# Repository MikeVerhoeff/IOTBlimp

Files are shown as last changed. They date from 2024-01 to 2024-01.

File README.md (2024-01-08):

# Folder Content

### /ArduinoExperimentCollection
- Java project to communicate with Adruino, and quickly plot the results
- Build with Maven and uses JavaFX and jSerialComm
- To run in Intellij open the Maven tab and run ArduinoExperimentCollection --> Plugins --> javafx --> javafx:run
- or run ```mvn clean javafx:run```

### /ArduinoExperimentCollection/scripts
- Python scripts that get run when data has been collected via the ui

### /ArduinoExperimentCollection/sensors
- Arduino project that implements the balloon failure detection

### /ArduinoExperimentCollection/ResultsIndex.ods
- Spreadsheet that has most/all the experiment that we did and where the data is stored

### /ArduinoExperimentCollection/scripts/overview/distrib2.py
- Script to generate plots

### /Sound detection 
- Scripts for testing the filter applied to the microphone

### /CAD
- 3D Model of the blimp drone mechanism

# Overview of Failure Detection Arduino Project

## Data Structures (SensorInterface.h)

For each set of sensors there is a SensorInterface that defines:
* a unique key (char), used in communication with UI
* a recognizable name of the group of sensors, displayed in UI
* a threshold value for when the balloon failure has to be triggered
* a function to initialize the sensors
* a function to stop the sensors
* a array (and its length) of TestInfo structs for each individual sensor

The TestInfo struct contains:
* function that returns current sensor value (short)
* values to construct the activation function (on, off, off2, on2, useonoff2)
* the weight of this sensor during fusion
* the time the highest value has to be held (hold_time)
* other values that get set and updated during detection(on_time, last_value, used_last_value)

## Detection loop (Settings.h)

The main loop for detecting balloon failure is in:

```void Settings.run_times(unsigned long n)```

This function runs the detection loop n times or forever if n=0 at the frequency that has been set before (default 175 Hz). It also turns on the LED when balloon failure has been detected and triggers the blimp to drone transformation.
It used ```short TestInfo.run(unsigned long current_time)``` to get the sensor value after passing through the activation function, and apply the hold time.

## General
```sensors.ino``` sets up all the sets of sensors that can be used and communicates with the UI.
```accelerometer.h```, ```gyroscope.h```, ```piezo.h```, ```proximity_sensor.h``` and ```microphone.h``` implement function to initialize, pole and stop the sensors. ```record.h``` has helper functions for printing results, and ```transform.h``` handles the servo that controls the clutch that caused the transformation when released.

# Overview of Data Collection UI

![image](UI.png)

The fist field "Python" sets the command used to execute the scripts in the directory set by "Script Directory".
The field "Data Directory" says where the results should be stored. "Experiment name" indicates how to name the folder with the results, if this field is left empty only a file with named with the current time is stored. If a Folder with the experiment name already exists "_(n)" is appended.

The dropdown box shows all serial interfaces after scanning. After connecting the next fields show up.
"Start Delay" sets a delay between pressing the start button and the start command being send.
After scanning "interface" selects which set of sensors(SensorInterface) to run.
"Frequency" sets and shows the frequency at which the sensors are checked.
"Time / Count" indicates how long to run the detection for. In "Time / (Count)" mode this value is in seconds, in "(Time) / Count" mode this value is in number of loops, in this mode if the value is set to 0 it will only stop when the stop button is pressed.

The Text Area "Serial" gets filled with the serial data the arduino sends after the it has indicated that it is done with the detection. The Text Area "Python" has the console output of the scripts, and gets all the images the scripts generate in there working directory.

## Command line arguments for scripts

Count: ```<python> <script file> <data file> -f <frequency> -c <count> -i <interface name>```

Time: ```<python> <script file> <data file> -f <frequency> -t <time> -i <interface name>```

# Plotting script

The plotting script `ArduinoExperimentCollection/scripts/overview/distrib2.py` can be used to generate plots used in the report for a specific sensor or quickly generate a plot for other data.
To generate the plots from the report run:
```
python distrib2.py MIC
python distrib2.py ACC
python distrib2.py PIEZO
python distrib2.py PROX
python distrib2.py FUSION
```
To generate other plots use:
```
python distrib.py <folder> <partial experiment name> <sensor name> <vals/max/min> ["filter"/no] [x label] [y label]
```
for example to plot the maximal values we got during our tests of fusion:
```
python distrib.py ../../pop fusion P_X max no "activation sum" "count / total"
```
This will get all the data from 'fusion', 'fusion_(1)', ..., 'fusion_(9)'.

This scrips also has some settings that can be set in the file:
```
hideHists = False      # don't display the histograms, only fit normal distributions
hideFit = True         # don't display 
dontShow = False       # don't open the graph in a window only store it
cumulative = True      # make a cumulative distribution from the histogram
showActivation = False # add the activation function
```

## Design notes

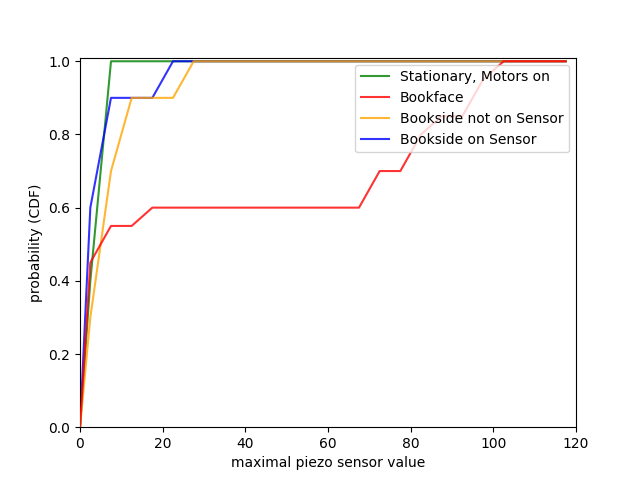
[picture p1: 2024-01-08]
ArduinoExperimentCollection/scripts/overview/hists/cdf/piezo_book_2.png

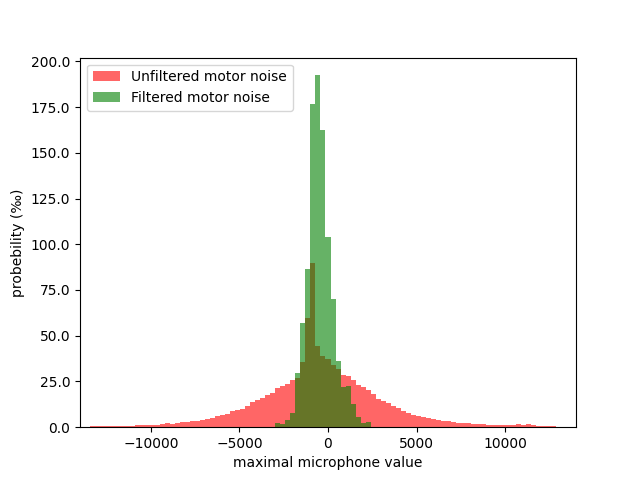
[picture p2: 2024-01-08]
ArduinoExperimentCollection/scripts/overview/hists/mic_noize.png

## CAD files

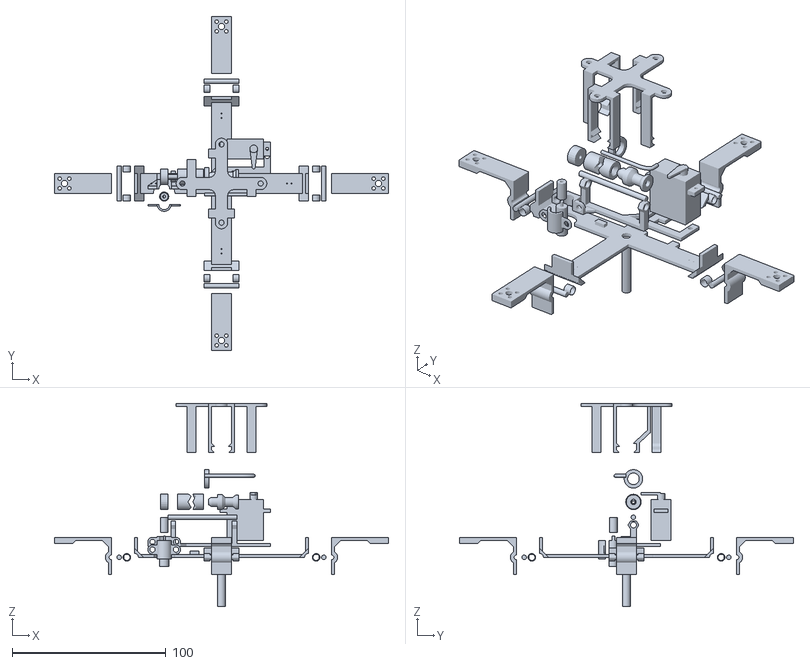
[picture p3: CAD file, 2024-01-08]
CAD/BlimpCoupling2_exploded.stl
217.0 x 217.0 x 132.0

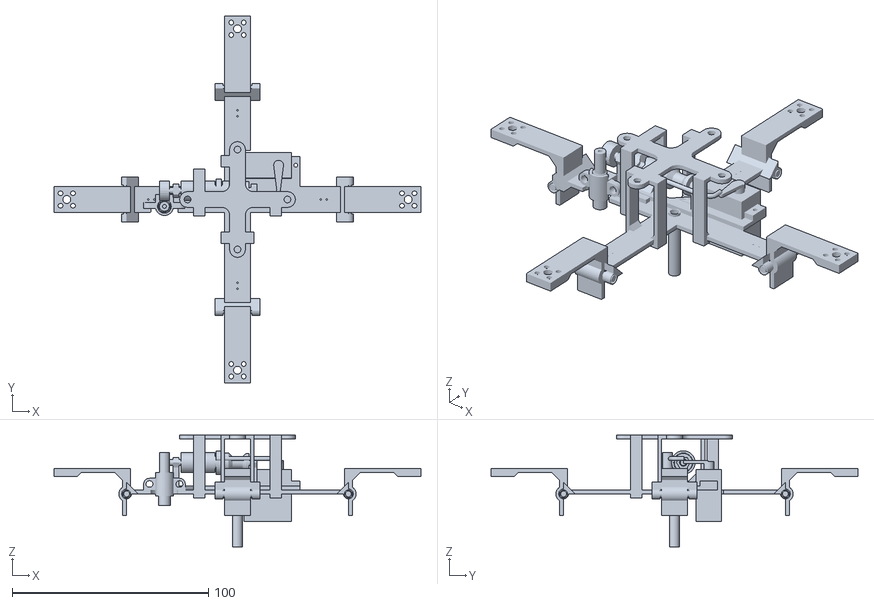
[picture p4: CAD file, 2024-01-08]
CAD/BlimpCoupling2.stl
187.0 x 187.0 x 57.0

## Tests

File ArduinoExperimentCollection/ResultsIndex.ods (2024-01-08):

Folder | Name | Description | balloon | Sensor | Graph
acc | fp_1ms_side | Moving drone side to side hanging on a string, abbout 1m/s, moving with arm | latex 30cm | ACC | Accelerometer: Movement
acc | fp_1ms_up_down | Moving drone up and down hanging on a string, moving with arm | latex 30cm | ACC | Accelerometer: Movement - Accelerometer: Pop
dataMic | 30cm_pop_filtered | Pop 21cm latex balllon 40 cm away | latex 50cm | MIC (f) | Microphone: Pop Balloon at Diffrent Distances
dataMic | 150cm_pop_filtered | Pop 21cm latex balllon 150 cm away | latex 50cm | MIC (f) | Microphone: Pop Balloon at Diffrent Distances
dataMic | 300hz_filtered | Play 300Hz tone on phone close above the microphone | none | MIC (f) | Microphone: Pop Balloon at Diffrent Distances
dataMic | still_filtered | Recording of quite room as baselline | none | MIC (f) | Microphone: Pop Balloon at Diffrent Distances
dataPartyBalloonPiezo\100K-PiezoFlex | * | Noticed the piezo has brocken, just recorded noize | latex 21cm | PIEZO
dataPartyBalloonPiezo\100K-PiozoHard-tapenormal | * | Prelimenary tests for the reenforced piezo sensor with 100K ohm resistor | latex 21cm | PIEZO | Piezo: Effect of Parallel Resistance(PiezoH_pop_(2), PiezoH_1M_pop) - Piezo: Hitting ballon in diffrent positions(PiezoH_pop) - Piezo: Distributions Scaled to Same Hieght(PiezoH_pop)
dataPartyBalloonPiezo\50K-PiozoHard-tapenormal | * | Prelimenary tests for the reenforced piezo sensor with 100K ohm resistor | latex 21cm | PIEZO | Piezo: Effect of Parallel Resistance(PiezoH_pop_(3))
dataPiezo | nerf_direct_hit | Shooting nerf disk at piezo sensor fixed to balloon | latex 50cm | PIEZO | Piezo: Hitting ballon in diffrent positions - Piezo: Distributions Scaled to Same Hieght
dataPiezo | nerf_disk_side | Shooting nerf disk at balloon, not hitting close to sensor | latex 50cm | PIEZO | Piezo: Hitting ballon in diffrent positions - Piezo: Distributions Scaled to Same Hieght
dataPiezo | still | Piezo sensor fixed to balloon, nothing happening | latex 50cm | PIEZO | Piezo: Maximal Value From 10 Runs: Still vs Vibrations - Piezo: Book Hits - Piezo: Distributions Scaled to Same Hieght
dataPiezo | vibration_dremel_5t | Using a dremmel set to 5000 rpm, with an uneven weighted attatchement to make the balloon vibrate | latex 50cm | PIEZO | Piezo: Maximal Value From 10 Runs: Still vs Vibrations
dataProx | baseline_absent | Recording sensor data without a balloon present | none | PROX | Proximity Balloon: Present vs Absent - Proximity Balloon: Absent - Proximity Balloon: Absent vs IR LED
dataProx | baseline_absent_<x> | Recording sensor data without a balloon present, but under specific lighting conditions <x> | none | PROX | Proximity Balloon: Present vs Absent - Proximity Balloon: Absent - Proximity Balloon: Absent vs IR LED
dataProx | gray_baseline_present | Recording sensor data with balloon present, and undisurbed | latex 50cm gray | PROX | Proximity Balloon: Present vs Absent - Proximity Balloon: Present vs Weaving Object
dataProx | gray_IR_LED_direct_full | https://www.adafruit.com/product/387 @ 1.6v pointing at arduino from just above it | latex 50cm gray | PROX | Proximity Balloon: Absent vs IR LED
dataProx | gray_IR_LED_indirect | https://www.adafruit.com/product/387 @ 1.6v pointing at the balloon just above the arduino | latex 50cm gray | PROX
dataProx | gray_stick | Move varius objects just above the sensor | latex 50cm gray | PROX | Proximity Balloon: Absent vs IR LED
dataProx | IR_LED_direct_under_powered | https://www.adafruit.com/product/387 @ 1.5v pointing at arduino from just above it | none | PROX | Proximity Balloon: Present vs Weaving Object
fp | 30cm_pop_filtered | Pop 21cm latex balllon 40 cm away | latex 50cm | MIC (f) | Microphone: Pop Balloon at Diffrent Distances
fp | 150cm_pop_filtered | Pop 21cm latex balllon 150 cm away | latex 50cm | MIC (f) | Microphone: Pop Balloon at Diffrent Distances
fp | black_plastic | Move black cap of super glue above sensor | latex 50cm gray | PROX | Proximity Balloon: Present vs Weaving Object
fp | permanent_marker | Move black whiteboard marker cap just above the sensor | latex 50cm gray | PROX | Proximity Balloon: Present vs Weaving Object - Proximity Balloon: Example of whiteboard marker interfearing(2)
fp | scissor | Move scissor just above the sensor | latex 50cm gray | PROX | Proximity Balloon: Present vs Weaving Object
fp | stick | Move satay sticks just above the sensor | latex 50cm gray | PROX | Proximity Balloon: Present vs Weaving Object
fp_tests | baseline_motor | Motors on at 50 or 60% recording all sensors, beging held still by holding balloon | tpu 21 inch | all | Piezo: Maximal Value From 10 Runs: Still vs Vibrations - Piezo: Distributions Scaled to Same Hieght - Accelerometer: Movement - Accelerometer: Pop
fp_tests | fp_1m | Pop 21cm latex balllon 1 m away | tpu 21 inch | MIC (r)
fp_tests | fp_10cm | Pop 21cm latex balllon 10 cm away | tpu 21 inch | MIC (r)
fp_tests | fp_black | Move black ballon up and down above sensor | latex 21cm | PROX
fp_tests | fp_gray | Move gray ballon up and down above sensor | latex 21cm | PROX
fp_tests | fp_red | Move red ballon up and down above sensor | latex 21cm | PROX | Proximity Balloon: Raise and Lower(6)
fp_tests | fp_transparent | Move transparent tpu ballon up and down above sensor | tpu 21 inch | PROX
fp_tests | fp_transparent_edge | Move transparent tpu ballon up and down above sensor, rotated that edge of ballon gows over sensor | tpu 21 inch | PROX | Proximity Balloon: Raise and Lower(5)
fp_tests | fp_transparent_blue | Move blue ballon up and down above sensor | latex 21cm | PROX
fp_tests | fp_white | Move white ballon up and down above sensor | latex 21cm | PROX
fp_tests | fp_mirror_angle | Move mirror up and down above sensor at 45 degree angle, so light is reflected away | none | PROX | Proximity Balloon: Raise and Lower(7)
fp_tests | fp_mirror_flat | Move mirror up and down above sensorf face down, so light is reflected back | none | PROX
fp_tests | fp_nerf_on | Shooting nerf disk at piezo sensor fixed to balloon | tpu 21 inch | PIEZO, ACC | Accelerometer: Movement
fp_tests | fp_nerf_non | Shooting nerf disk at balloon, not hitting close to sensor | tpu 21 inch | PIEZO, ACC | Accelerometer: Movement
fp_tests | fp_bookface_soft | Hitting ballon with the face of a book, random position | tpu 21 inch | PIEZO, ACC | Piezo: Book Hits - Accelerometer: Movement
fp_tests | fp_bookside_non | Hitting ballon with the face of a book, random position, but not on piezo sensor | tpu 21 inch | PIEZO, ACC | Piezo: Book Hits - Accelerometer: Movement
fp_tests | fp_bookside_on | Hitting ballon with the face of a book, close to piezo sensor | tpu 21 inch | PIEZO, ACC | Piezo: Book Hits - Accelerometer: Movement
pop | acc | Pop balloon to determine responce time | latex 50cm | ACC | Accelerometer: Pop
pop | mic | Pop balloon to determine responce time | latex 50cm | MIC (f) | Microphone: Pop Balloon at Diffrent Distances
pop | piezo | Pop balloon to determine responce time | latex 50cm | PIEZO | Piezo: Hitting ballon in diffrent positions
pop | fusion | Pop balloon to determine responce time and reliability of fusion | latex 50cm | PIEZO(breaking), ACC, PROX | Piezo: Hitting ballon in diffrent positions, Accelerometer: Pop
pop | all | Pop balloon to determine fusion weight | latex 50cm | all (PIEZO is breaking) | Proximity Balloon: Examples of popping(1, 7, 8) - Accelerometer: Pop - Microphone: Pop Balloon at Diffrent Distances - Piezo: Hitting ballon in diffrent positions
pop | "all", "all_(3)", "all_(4)" | Pop balloon to determine fusion weight | latex 30cm | all (PIEZO is breaking) | Accelerometer: Pop - Microphone: Pop Balloon at Diffrent Distances
pop | all_small | Pop balloon to determine fusion weight | latex 21cm | all | Microphone: Pop Balloon at Diffrent Distances
prelim_tests | pie_face_hard_non |  | tpu 21 inch | PIEZO
prelim_tests | pie_face_soft_non |  | tpu 21 inch | PIEZO
prelim_tests | pie_motor_side |  | tpu 21 inch | PIEZO
prelim_tests | pie_motor_side_tran |  | tpu 21 inch | PIEZO
prelim_tests | pie_motor_side45 |  | tpu 21 inch | PIEZO
prelim_tests | pie_nerf_dart_non | Shoot nerf dart at senor point blank | tpu 21 inch | PIEZO
prelim_tests | pie_nerf_dart_non_soft | Shoot nerf dart at senor further away | tpu 21 inch | PIEZO
prelim_tests | pie_nerf_disk_non_hard | Shoot nerf disk at senor point blank | tpu 21 inch | PIEZO
prelim_tests | pie_nerf_disk_on_hard | Shoot nerf disk at senor further away | tpu 21 inch | PIEZO
prelim_tests | pie_pop | Pop tpu balloon | tpu 21 inch | PIEZO
prelim_tests | pie_side_hard_non |  | tpu 21 inch | PIEZO
prelim_tests | pie_side_soft_non |  | tpu 21 inch | PIEZO
prelim_tests | prox_tran_test |  | tpu 21 inch | PROX
small_pop | p_not_stuck | Ballon pop not taped to drone | latex 21cm | PIEZO
small_pop | piezo | Ballon pop taped to drone | latex 21cm | PIEZO

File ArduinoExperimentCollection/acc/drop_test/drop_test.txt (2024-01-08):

P_X:
0
0
0
0
0
0
0
0
0
0
0
0
0
0
0
0
0
0
0
0
0
0
0
0
0
0
0
0
0
0
0
0
0
0
0
0
0
0
0
0
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
ACC_X:
0.17
0.17
0.17
0.14
0.14
0.14
0.13
0.13
0.12
0.12
0.10
0.10
0.07
0.06
0.06
0.06
0.06
0.05
0.05
0.04
0.05
0.05
0.07
0.07
0.12
0.12
0.15
0.15
0.15
0.13
0.13
0.08
0.08
0.04
0.02
0.02
0.06
0.06
0.13
0.13
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
ACC_Y:
0.24
-0.16
-0.16
-0.15
-0.15
-0.15
0.12
0.12
0.20
0.20
0.19
0.19
0.11
-0.03
-0.03
-0.16
-0.16
-0.19
-0.19
-0.11
-0.02
-0.02
0.01
0.01
-0.05
-0.05
-0.17
-0.29
-0.29
-0.35
-0.35
-0.36
-0.36
-0.33
-0.23
-0.23
-0.08
-0.08
0.05
0.05
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
ACC_Z:
1.78
0.64
0.64
0.69
0.69
0.69
0.70
0.70
0.78
0.78
0.83
0.83
0.79
0.66
0.66
0.61
0.61
0.69
0.69
0.75
0.76
0.76
0.82
0.82
0.98
0.98
1.08
1.01
1.01
0.90
0.90
0.92
0.92
1.02
1.03
1.03
0.96
0.96
0.89
0.89
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

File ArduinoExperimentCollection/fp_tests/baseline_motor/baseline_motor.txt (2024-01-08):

ACC_X:
-0.14
-0.15
-0.15
-0.15
-0.14
-0.13
-0.13
-0.14
-0.14
-0.14
-0.14
-0.14
-0.14
-0.13
-0.13
-0.11
-0.11
-0.13
-0.13
-0.15
-0.15
-0.14
-0.14
-0.14
-0.12
-0.12
-0.12
-0.12
-0.12
-0.12
-0.13
-0.13
-0.14
-0.13
-0.13
-0.14
-0.14
-0.15
-0.15
-0.15
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
ACC_Y:
-0.09
-0.09
-0.06
-0.06
-0.07
-0.07
-0.07
-0.11
-0.11
-0.10
-0.10
-0.11
-0.11
-0.10
-0.10
-0.06
-0.06
-0.07
-0.07
-0.08
-0.08
-0.10
-0.12
-0.12
-0.08
-0.08
-0.06
-0.06
-0.05
-0.05
-0.10
-0.10
-0.15
-0.12
-0.12
-0.08
-0.08
-0.06
-0.06
-0.12
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
ACC_Z:
0.98
1.00
1.01
1.01
1.00
0.98
0.98
0.96
0.96
0.97
0.97
0.95
0.95
0.96
0.96
0.99
0.99
0.99
0.99
1.00
1.00
0.98
0.98
0.98
0.99
0.99
0.98
0.98
1.00
1.00
0.97
0.97
0.96
0.98
0.98
0.97
0.97
1.00
1.00
1.00
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
PIEZO:
2.00
0.00
0.00
1.00
2.00
0.00
0.00
0.00
0.00
1.00
0.00
0.00
0.00
0.00
2.00
0.00
1.00
0.00
2.00
0.00
0.00
1.00
0.00
0.00
0.00
0.00
0.00
3.00
0.00
0.00
0.00
3.00
0.00
0.00
0.00
3.00
0.00
1.00
0.00
2.00
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
MIC:
-1001
2692
808
1968
534
2612
3017
1648
1875
-27
791
735
308
79
577
1862
592
997
-1485
-45
-2870
-857
-894
-2852
92
1904
1658
-3743
-1389
-1066
-1463
-3076
-1706
1292
-1340
72
492
2328
370
-944
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
PROXIMITY:
0
0
0
0
0
0
0
0
0
0
0
0
0
0
0
0
0
0
0
0
0
0
0
0
0
0
0
0
0
0
0
0
0
0
0
0
0
0
0
0
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

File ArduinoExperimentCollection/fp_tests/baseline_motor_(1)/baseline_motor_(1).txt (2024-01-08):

ACC_X:
-0.15
-0.13
-0.13
-0.13
-0.13
-0.13
-0.13
-0.13
-0.13
-0.14
-0.14
-0.14
-0.14
-0.14
-0.14
-0.14
-0.14
-0.13
-0.13
-0.14
-0.14
-0.15
-0.15
-0.15
-0.15
-0.15
-0.14
-0.14
-0.15
-0.15
-0.15
-0.15
-0.14
-0.14
-0.12
-0.12
-0.12
-0.12
-0.12
-0.12
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
ACC_Y:
-0.10
-0.12
-0.12
-0.12
-0.08
-0.08
-0.07
-0.07
-0.11
-0.10
-0.10
-0.08
-0.08
-0.10
-0.10
-0.10
-0.10
-0.13
-0.13
-0.16
-0.16
-0.10
-0.10
-0.08
-0.08
-0.08
-0.07
-0.07
-0.11
-0.11
-0.14
-0.14
-0.10
-0.10
-0.09
-0.09
-0.09
-0.09
-0.09
-0.12
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
ACC_Z:
0.96
0.99
0.98
0.98
1.00
1.00
1.01
1.01
0.99
1.00
1.00
1.01
1.01
0.99
0.99
1.00
1.00
0.99
0.99
0.97
0.97
1.00
1.00
1.00
1.00
0.99
1.00
1.00
1.00
1.00
0.98
0.98
0.98
0.98
0.98
0.98
0.98
0.98
0.98
0.99
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
PIEZO:
0.00
0.00
0.00
0.00
0.00
0.00
2.00
0.00
0.00
0.00
0.00
0.00
1.00
0.00
0.00
0.00
0.00
0.00
0.00
0.00
1.00
2.00
0.00
2.00
0.00
1.00
0.00
0.00
2.00
0.00
0.00
1.00
0.00
0.00
0.00
0.00
0.00
0.00
2.00
0.00
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
MIC:
2742
-2150
-577
345
1712
902
-338
-1095
1230
1094
-2346
-5163
2271
-2026
1176
1505
-445
491
-922
2179
1957
-986
-2109
-56
2208
790
-692
1915
-579
1192
-6708
-1216
-1233
-1511
-511
-2273
-1739
-3553
-2940
342
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
PROXIMITY:
0
0
0
0
0
0
0
0
0
0
0
0
0
0
0
0
0
0
0
0
0
0
0
0
0
0
0
0
0
0
0
0
0
0
0
0
0
0
0
0
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

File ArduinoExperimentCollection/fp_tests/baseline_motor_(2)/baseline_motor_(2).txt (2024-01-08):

ACC_X:
-0.09
-0.11
-0.10
-0.10
-0.10
-0.11
-0.11
-0.09
-0.09
-0.09
-0.09
-0.10
-0.10
-0.10
-0.10
-0.09
-0.09
-0.10
-0.10
-0.10
-0.10
-0.10
-0.13
-0.12
-0.12
-0.11
-0.11
-0.12
-0.12
-0.12
-0.12
-0.11
-0.11
-0.11
-0.11
-0.11
-0.11
-0.11
-0.11
-0.11
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
ACC_Y:
-0.12
-0.07
-0.12
-0.12
-0.15
-0.11
-0.11
-0.09
-0.09
-0.09
-0.09
-0.07
-0.07
-0.06
-0.06
-0.10
-0.10
-0.13
-0.13
-0.13
-0.13
-0.13
-0.11
-0.10
-0.10
-0.12
-0.12
-0.14
-0.14
-0.11
-0.11
-0.07
-0.07
-0.08
-0.08
-0.11
-0.11
-0.09
-0.09
-0.09
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
ACC_Z:
0.95
1.01
0.98
0.98
0.98
0.99
0.99
0.99
0.99
0.97
0.97
0.99
0.99
1.00
1.00
0.99
0.99
0.97
0.97
0.97
0.97
0.97
1.00
1.00
1.00
0.98
0.98
0.98
0.98
1.00
1.00
1.01
1.01
1.00
1.00
0.99
0.99
1.00
1.00
1.00
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
PIEZO:
0.00
2.00
0.00
1.00
1.00
0.00
0.00
0.00
0.00
0.00
1.00
2.00
0.00
1.00
0.00
0.00
0.00
0.00
0.00
0.00
0.00
0.00
2.00
0.00
0.00
0.00
0.00
2.00
0.00
0.00
0.00
1.00
0.00
0.00
0.00
0.00
0.00
0.00
0.00
2.00
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
MIC:
-849
-1592
184
-1407
-1340
-2628
-2704
-1794
89
123
352
-3438
-3333
-2701
33
-5830
-3097
-813
-1533
-1778
-1277
-390
-3712
-2101
-2130
-2034
-3533
-1884
-32
883
-99
-1289
-2190
-1052
-727
-4286
-1160
2
-588
1049
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
PROXIMITY:
0
0
0
0
0
0
0
0
0
0
0
0
0
0
0
0
0
0
0
0
0
0
0
0
0
0
0
0
0
0
0
0
0
0
0
0
0
0
0
0
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

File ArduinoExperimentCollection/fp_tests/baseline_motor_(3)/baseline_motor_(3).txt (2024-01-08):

ACC_X:
-0.13
-0.15
-0.14
-0.14
-0.15
-0.15
-0.15
-0.15
-0.15
-0.14
-0.14
-0.14
-0.14
-0.12
-0.13
-0.13
-0.13
-0.13
-0.13
-0.13
-0.13
-0.13
-0.13
-0.13
-0.14
-0.13
-0.13
-0.15
-0.15
-0.15
-0.15
-0.15
-0.15
-0.18
-0.18
-0.16
-0.16
-0.14
-0.14
-0.13
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
ACC_Y:
-0.06
-0.13
-0.11
-0.11
-0.08
-0.08
-0.08
-0.08
-0.08
-0.07
-0.07
-0.08
-0.08
-0.09
-0.11
-0.11
-0.08
-0.08
-0.10
-0.10
-0.08
-0.08
-0.04
-0.04
-0.04
-0.08
-0.08
-0.12
-0.12
-0.15
-0.15
-0.17
-0.17
-0.12
-0.12
-0.07
-0.07
-0.03
-0.03
-0.05
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
ACC_Z:
0.97
0.98
0.98
0.98
0.99
0.99
0.99
0.99
0.99
0.99
0.99
0.99
0.99
0.98
0.98
0.98
0.99
0.99
0.97
0.97
0.99
0.99
0.99
0.99
0.98
0.99
0.99
0.98
0.98
0.99
0.99
0.98
0.98
1.01
1.01
1.01
1.01
0.98
0.98
0.98
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
PIEZO:
3.00
0.00
0.00
3.00
0.00
0.00
0.00
1.00
0.00
0.00
0.00
0.00
0.00
0.00
0.00
0.00
0.00
0.00
0.00
0.00
0.00
2.00
0.00
0.00
2.00
3.00
0.00
1.00
0.00
1.00
0.00
0.00
0.00
0.00
0.00
0.00
2.00
0.00
0.00
0.00
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
MIC:
1070
-385
1937
3332
3144
2710
3242
5800
5843
4345
4926
6339
3399
2422
1583
1805
2445
2208
4024
3821
2669
370
-1899
-361
869
-275
891
2617
4201
4403
2790
3219
4136
4211
1845
4467
1238
3471
4133
5225
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
PROXIMITY:
0
0
0
0
0
0
0
0
0
0
0
0
0
0
0
0
0
0
0
0
0
0
0
0
0
0
0
0
0
0
0
0
0
0
0
0
0
0
0
0
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

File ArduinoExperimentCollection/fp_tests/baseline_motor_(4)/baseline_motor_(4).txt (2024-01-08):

ACC_X:
-0.14
-0.15
-0.15
-0.15
-0.14
-0.14
-0.14
-0.14
-0.14
-0.14
-0.14
-0.15
-0.15
-0.14
-0.14
-0.14
-0.14
-0.14
-0.14
-0.14
-0.14
-0.15
-0.15
-0.14
-0.14
-0.14
-0.14
-0.14
-0.14
-0.14
-0.15
-0.15
-0.15
-0.16
-0.16
-0.15
-0.15
-0.15
-0.15
-0.14
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
ACC_Y:
-0.10
-0.09
-0.07
-0.07
-0.08
-0.08
-0.08
-0.08
-0.08
-0.10
-0.10
-0.11
-0.11
-0.11
-0.11
-0.11
-0.11
-0.11
-0.11
-0.11
-0.11
-0.10
-0.10
-0.14
-0.14
-0.15
-0.15
-0.15
-0.15
-0.15
-0.09
-0.10
-0.10
-0.12
-0.12
-0.13
-0.13
-0.12
-0.12
-0.09
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
ACC_Z:
0.97
0.98
0.98
0.98
0.98
0.98
0.98
0.98
0.98
0.99
0.99
0.99
0.99
0.99
0.99
0.99
0.99
0.99
0.99
0.99
0.99
0.97
0.97
0.96
0.96
0.98
0.98
0.98
0.98
0.98
0.99
0.99
0.99
0.99
0.99
0.98
0.98
0.99
0.99
0.99
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
PIEZO:
0.00
1.00
0.00
0.00
0.00
2.00
0.00
0.00
2.00
0.00
0.00
0.00
1.00
0.00
0.00
0.00
0.00
1.00
0.00
0.00
1.00
0.00
1.00
0.00
1.00
0.00
0.00
2.00
0.00
0.00
0.00
1.00
1.00
0.00
1.00
0.00
0.00
1.00
3.00
0.00
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
MIC:
198
-4120
1474
-1996
-178
-2880
-2813
1614
-1323
-384
28
-1502
-2957
616
-1222
2602
3769
3363
-4499
-1770
-613
-1585
-1549
-2413
-847
160
-3804
-1368
-2170
-728
1446
-37
-588
334
-1126
1466
5726
5252
-2630
-2196
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
PROXIMITY:
0
0
0
0
0
0
0
0
0
0
0
0
0
0
0
0
0
0
0
0
0
0
0
0
0
0
0
0
0
0
0
0
0
0
0
0
0
0
0
0
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

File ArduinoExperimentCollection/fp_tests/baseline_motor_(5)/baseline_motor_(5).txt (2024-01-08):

ACC_X:
-0.15
-0.15
-0.14
-0.14
-0.14
-0.14
-0.15
-0.15
-0.14
-0.15
-0.15
-0.15
-0.15
-0.14
-0.14
-0.14
-0.14
-0.13
-0.13
-0.16
-0.16
-0.16
-0.16
-0.16
-0.16
-0.15
-0.12
-0.12
-0.14
-0.14
-0.16
-0.16
-0.16
-0.16
-0.15
-0.15
-0.14
-0.15
-0.15
-0.15
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
ACC_Y:
-0.08
-0.14
-0.12
-0.12
-0.09
-0.09
-0.10
-0.10
-0.10
-0.13
-0.13
-0.12
-0.12
-0.11
-0.11
-0.10
-0.10
-0.09
-0.09
-0.12
-0.12
-0.12
-0.12
-0.14
-0.14
-0.13
-0.08
-0.08
-0.10
-0.10
-0.13
-0.13
-0.17
-0.17
-0.14
-0.14
-0.09
-0.10
-0.10
-0.12
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
ACC_Z:
0.99
0.99
0.99
0.99
0.98
0.98
0.99
0.99
0.99
0.98
0.98
0.99
0.99
0.98
0.98
0.99
0.99
0.99
0.99
0.97
0.97
0.98
0.98
0.97
0.97
0.98
0.98
0.98
0.97
0.97
0.99
0.99
0.97
0.97
0.97
0.97
0.97
0.97
0.97
0.99
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
PIEZO:
0.00
1.00
2.00
1.00
1.00
0.00
0.00
0.00
0.00
0.00
5.00
0.00
0.00
0.00
0.00
0.00
0.00
1.00
1.00
0.00
0.00
0.00
2.00
1.00
3.00
0.00
3.00
0.00
2.00
0.00
0.00
0.00
0.00
1.00
3.00
1.00
0.00
0.00
1.00
2.00
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
MIC:
-3086
-1441
1793
1701
-110
-729
-787
3340
670
-853
1270
1897
2437
-19
-483
965
1810
199
3295
4968
159
2691
2007
-494
594
-1934
860
-1048
5
-658
-1493
1508
43
1613
1020
-846
-2944
-2923
5
2321
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
PROXIMITY:
0
0
0
0
0
0
0
0
0
0
0
0
0
0
0
0
0
0
0
0
0
0
0
0
0
0
0
0
0
0
0
0
0
0
0
0
0
0
0
0
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

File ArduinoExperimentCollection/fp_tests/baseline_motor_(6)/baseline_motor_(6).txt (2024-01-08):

ACC_X:
-0.14
-0.15
-0.14
-0.14
-0.14
-0.14
-0.14
-0.14
-0.14
-0.15
-0.15
-0.15
-0.15
-0.15
-0.15
-0.15
-0.15
-0.15
-0.15
-0.16
-0.16
-0.16
-0.16
-0.16
-0.16
-0.15
-0.15
-0.14
-0.14
-0.15
-0.15
-0.15
-0.15
-0.14
-0.14
-0.14
-0.14
-0.14
-0.15
-0.15
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
ACC_Y:
-0.12
-0.09
-0.07
-0.07
-0.07
-0.07
-0.07
-0.07
-0.07
-0.12
-0.12
-0.13
-0.13
-0.10
-0.10
-0.10
-0.10
-0.10
-0.07
-0.08
-0.08
-0.12
-0.12
-0.13
-0.13
-0.14
-0.14
-0.12
-0.12
-0.11
-0.11
-0.08
-0.08
-0.07
-0.07
-0.07
-0.07
-0.07
-0.14
-0.15
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
ACC_Z:
0.97
0.99
0.99
0.99
0.98
0.98
0.98
0.98
0.98
0.98
0.98
0.99
0.99
0.99
0.99
0.99
0.99
0.99
0.99
1.00
1.00
0.99
0.99
1.00
1.00
1.00
1.00
0.98
0.98
0.98
0.98
0.97
0.97
0.98
0.98
0.98
0.98
0.98
0.98
0.97
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
PIEZO:
2.00
1.00
0.00
2.00
2.00
0.00
1.00
0.00
0.00
3.00
2.00
0.00
0.00
0.00
0.00
0.00
1.00
0.00
0.00
0.00
0.00
0.00
0.00
0.00
0.00
0.00
0.00
0.00
0.00
0.00
0.00
0.00
0.00
0.00
0.00
1.00
0.00
0.00
3.00
0.00
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
MIC:
-4796
-4664
-4330
-4190
-7286
-6817
-6860
-5267
-2073
-1806
-5175
-3436
-4381
-4894
-4621
-4566
-4421
-2506
-3977
-3787
-5213
-4205
-1349
-3826
-5262
-10201
-4871
-1715
-1542
-79
-2421
-4903
-3482
-3560
-3933
-2371
-435
-1869
-1197
-4050
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
PROXIMITY:
0
0
0
0
0
0
0
0
0
0
0
0
0
0
0
0
0
0
0
0
0
0
0
0
0
0
0
0
0
0
0
0
0
0
0
0
0
0
0
0
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

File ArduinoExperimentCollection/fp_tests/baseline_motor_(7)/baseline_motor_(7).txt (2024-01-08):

ACC_X:
-0.13
-0.16
-0.15
-0.15
-0.15
-0.16
-0.16
-0.17
-0.17
-0.16
-0.16
-0.15
-0.15
-0.14
-0.14
-0.14
-0.14
-0.14
-0.14
-0.14
-0.14
-0.15
-0.14
-0.14
-0.14
-0.14
-0.15
-0.15
-0.18
-0.18
-0.17
-0.17
-0.14
-0.13
-0.13
-0.13
-0.13
-0.14
-0.14
-0.14
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
ACC_Y:
-0.12
-0.10
-0.09
-0.09
-0.11
-0.17
-0.17
-0.18
-0.18
-0.13
-0.13
-0.08
-0.08
-0.06
-0.06
-0.10
-0.10
-0.14
-0.14
-0.14
-0.14
-0.12
-0.10
-0.10
-0.10
-0.10
-0.11
-0.11
-0.14
-0.14
-0.14
-0.14
-0.09
-0.05
-0.05
-0.07
-0.07
-0.10
-0.10
-0.13
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
ACC_Z:
0.97
0.97
0.97
0.97
0.96
0.98
0.98
0.98
0.98
1.00
1.00
1.00
1.00
1.01
1.01
1.01
1.01
1.01
1.01
0.99
0.99
0.98
0.97
0.97
0.96
0.96
0.98
0.98
0.98
0.98
1.00
1.00
1.00
1.01
1.01
0.99
0.99
0.97
0.97
0.98
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
PIEZO:
1.00
1.00
0.00
1.00
0.00
4.00
0.00
0.00
0.00
0.00
1.00
2.00
0.00
1.00
2.00
2.00
0.00
1.00
0.00
0.00
0.00
0.00
0.00
2.00
0.00
1.00
0.00
0.00
0.00
2.00
0.00
0.00
0.00
0.00
0.00
0.00
0.00
2.00
1.00
0.00
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
MIC:
9795
11114
8721
8797
8779
10079
11151
11060
7540
9657
9580
7641
7562
8011
6434
7194
5919
4479
539
4183
3853
7012
4548
4264
5259
2433
6560
4677
4921
6986
7713
6124
6495
7099
7659
11151
9713
8692
628
3404
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
PROXIMITY:
0
0
0
0
0
0
0
0
0
0
0
0
0
0
0
0
0
0
0
0
0
0
0
0
0
0
0
0
0
0
0
0
0
0
0
0
0
0
0
0
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

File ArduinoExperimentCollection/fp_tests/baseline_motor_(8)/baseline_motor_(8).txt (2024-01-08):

ACC_X:
-0.11
-0.09
-0.07
-0.07
-0.09
-0.10
-0.10
-0.10
-0.10
-0.09
-0.09
-0.09
-0.09
-0.09
-0.09
-0.09
-0.09
-0.10
-0.10
-0.11
-0.11
-0.11
-0.11
-0.11
-0.10
-0.09
-0.09
-0.08
-0.08
-0.10
-0.10
-0.10
-0.10
-0.09
-0.09
-0.09
-0.09
-0.09
-0.09
-0.09
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
ACC_Y:
-0.09
-0.14
-0.16
-0.16
-0.12
-0.09
-0.09
-0.08
-0.08
-0.13
-0.13
-0.16
-0.16
-0.16
-0.16
-0.16
-0.16
-0.12
-0.12
-0.12
-0.12
-0.12
-0.12
-0.12
-0.14
-0.16
-0.16
-0.15
-0.15
-0.11
-0.11
-0.08
-0.08
-0.11
-0.11
-0.15
-0.15
-0.16
-0.16
-0.14
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
ACC_Z:
0.98
0.99
0.98
0.98
0.99
0.98
0.98
0.98
0.98
0.98
0.98
0.97
0.97
0.98
0.98
0.98
0.98
0.99
0.99
0.99
0.99
0.99
0.99
0.99
1.00
1.00
1.00
1.00
1.00
1.00
1.00
1.00
1.00
0.97
0.97
0.97
0.97
0.97
0.97
0.99
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
PIEZO:
0.00
0.00
1.00
0.00
0.00
1.00
1.00
0.00
0.00
0.00
0.00
1.00
0.00
2.00
0.00
1.00
0.00
0.00
1.00
1.00
0.00
1.00
1.00
0.00
0.00
0.00
4.00
0.00
0.00
2.00
0.00
0.00
3.00
0.00
0.00
0.00
2.00
2.00
0.00
0.00
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
MIC:
1505
-1080
-800
1145
900
3826
5559
9054
5551
1982
3396
3258
3819
6898
-129
4771
6667
6979
6363
5323
9496
5401
5328
4868
5288
3207
5103
8652
7292
2195
167
3808
6189
4332
-2461
2940
3337
5657
4892
4871
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
PROXIMITY:
0
0
0
0
0
0
0
0
0
0
0
0
0
0
0
0
0
0
0
0
0
0
0
0
0
0
0
0
0
0
0
0
0
0
0
0
0
0
0
0
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

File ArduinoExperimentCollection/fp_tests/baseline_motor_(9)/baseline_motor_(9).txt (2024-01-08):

ACC_X:
-0.12
-0.15
-0.17
-0.17
-0.16
-0.16
-0.13
-0.13
-0.10
-0.10
-0.10
-0.10
-0.10
-0.14
-0.14
-0.14
-0.14
-0.13
-0.12
-0.12
-0.14
-0.14
-0.16
-0.16
-0.17
-0.17
-0.14
-0.14
-0.11
-0.11
-0.11
-0.11
-0.11
-0.12
-0.12
-0.14
-0.14
-0.12
-0.12
-0.12
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
ACC_Y:
-0.12
-0.14
-0.16
-0.16
-0.17
-0.17
-0.15
-0.15
-0.11
-0.11
-0.11
-0.11
-0.11
-0.13
-0.13
-0.14
-0.14
-0.13
-0.15
-0.15
-0.19
-0.19
-0.18
-0.18
-0.12
-0.12
-0.08
-0.08
-0.11
-0.11
-0.11
-0.11
-0.11
-0.22
-0.22
-0.14
-0.14
-0.05
-0.05
-0.05
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
ACC_Z:
0.97
0.97
1.00
1.00
1.02
1.02
1.01
1.01
0.97
0.97
0.97
0.97
0.97
0.99
0.99
1.01
1.01
0.98
0.94
0.94
0.95
0.95
1.01
1.01
1.05
1.05
1.02
1.02
0.95
0.95
0.95
0.95
0.95
0.97
0.97
1.01
1.01
1.01
0.97
0.97
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
PIEZO:
0.00
0.00
0.00
0.00
0.00
0.00
0.00
0.00
0.00
0.00
2.00
1.00
4.00
0.00
0.00
0.00
0.00
0.00
2.00
0.00
0.00
0.00
0.00
0.00
1.00
0.00
1.00
0.00
2.00
1.00
0.00
0.00
0.00
0.00
1.00
0.00
0.00
0.00
2.00
0.00
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
MIC:
-1092
947
-1095
-271
-471
570
-2533
-900
1353
1297
-537
-1159
-1359
239
-1654
15
1554
-1286
-1837
-830
-1182
-872
1001
929
-904
415
-3777
-1148
-1160
265
-591
-1091
771
691
1050
2468
3473
418
-275
-2505
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
PROXIMITY:
0
0
0
0
0
0
0
0
0
0
0
0
0
0
0
0
0
0
0
0
0
0
0
0
0
0
0
0
0
0
0
0
0
0
0
0
0
0
0
0
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

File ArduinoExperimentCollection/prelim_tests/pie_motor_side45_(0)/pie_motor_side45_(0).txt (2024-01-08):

PIEZO1:
0.00
0.00
0.00
0.00
0.00
0.00
0.00
0.00
0.00
0.00
0.00
0.00
0.00
0.00
0.00
0.00
0.00
0.00
0.00
0.00
0.00
0.00
0.00
0.00
0.00
0.00
0.00
0.00
0.00
0.00
0.00
0.00
0.00
0.00
0.00
0.00
0.00
0.00
0.00
0.00
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
PIEZO2:
0.00
0.00
0.00
0.00
0.00
0.00
0.00
0.00
0.00
0.00
0.00
0.00
0.00
0.00
0.00
0.00
0.00
0.00
0.00
0.00
0.00
0.00
0.00
0.00
0.00
0.00
0.00
0.00
0.00
0.00
0.00
0.00
0.00
0.00
0.00
0.00
0.00
0.00
0.00
0.00
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

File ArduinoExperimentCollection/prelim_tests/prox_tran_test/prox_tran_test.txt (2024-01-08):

PROXIMITY:
0
0
0
0
0
0
0
0
0
0
0
0
0
0
0
0
0
0
0
0
0
0
0
0
0
0
0
0
0
0
0
0
0
0
0
0
0
0
0
0
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

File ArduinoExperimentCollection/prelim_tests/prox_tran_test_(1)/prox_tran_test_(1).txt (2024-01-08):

PROXIMITY:
0
0
0
0
0
0
0
0
0
0
0
0
0
0
0
0
0
0
0
0
0
0
0
0
0
0
0
0
0
0
0
0
0
0
0
0
0
0
0
0
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

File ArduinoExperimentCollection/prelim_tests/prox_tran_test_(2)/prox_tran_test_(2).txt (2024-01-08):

PROXIMITY:
0
0
0
0
0
0
0
0
0
0
0
0
0
0
0
0
0
0
0
0
0
0
0
0
0
0
0
0
0
0
0
0
0
0
0
0
0
0
0
0
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

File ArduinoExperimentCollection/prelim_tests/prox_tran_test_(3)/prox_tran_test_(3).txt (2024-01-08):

PROXIMITY:
0
0
0
0
0
0
0
0
0
0
0
0
0
0
0
0
0
0
0
0
0
0
0
0
0
0
0
0
0
0
0
0
0
0
0
0
0
0
0
0
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

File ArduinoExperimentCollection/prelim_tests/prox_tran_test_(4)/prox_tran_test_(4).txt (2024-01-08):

PROXIMITY:
0
0
0
0
0
0
0
0
0
0
0
0
0
0
0
0
0
0
0
0
0
0
0
0
0
0
0
0
0
0
0
0
0
0
0
0
0
0
0
0
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

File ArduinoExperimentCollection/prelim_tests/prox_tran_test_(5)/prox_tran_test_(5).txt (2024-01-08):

PROXIMITY:
0
0
0
0
0
0
0
0
0
0
0
0
0
0
0
0
0
0
0
0
0
0
0
0
0
0
0
0
0
0
0
0
0
0
0
0
0
0
0
0
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

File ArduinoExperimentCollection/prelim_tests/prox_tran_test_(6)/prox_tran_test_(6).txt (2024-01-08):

PROXIMITY:
0
0
0
0
0
0
0
0
0
0
0
0
0
0
0
0
0
0
0
0
0
0
0
0
0
0
0
0
0
0
0
0
0
0
0
0
0
0
0
0
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

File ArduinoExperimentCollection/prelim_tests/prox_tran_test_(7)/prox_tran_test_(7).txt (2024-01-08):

PROXIMITY:
0
0
0
0
0
0
0
0
0
0
0
0
0
0
0
0
0
0
0
0
0
0
0
0
0
0
0
0
0
0
0
0
0
0
0
0
0
0
0
0
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

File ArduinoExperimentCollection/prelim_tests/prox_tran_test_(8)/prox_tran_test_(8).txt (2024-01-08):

PROXIMITY:
0
0
0
0
0
0
0
0
0
0
0
0
0
0
0
0
0
0
0
0
0
0
0
0
0
0
0
0
0
0
0
0
0
0
0
0
0
0
0
0
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

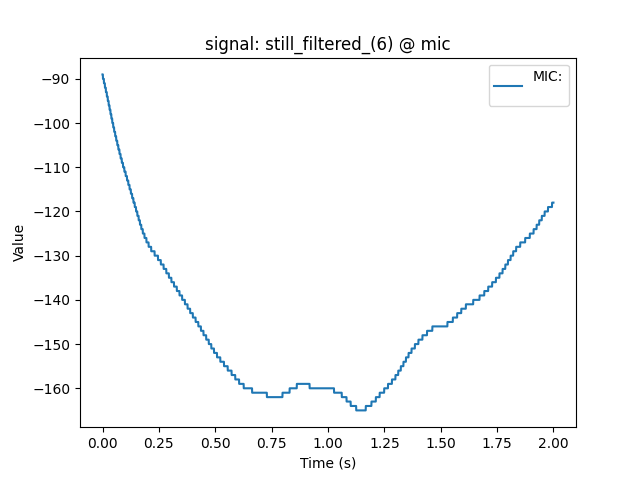
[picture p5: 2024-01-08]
ArduinoExperimentCollection/dataMic/still_filtered_(6)/signal.png

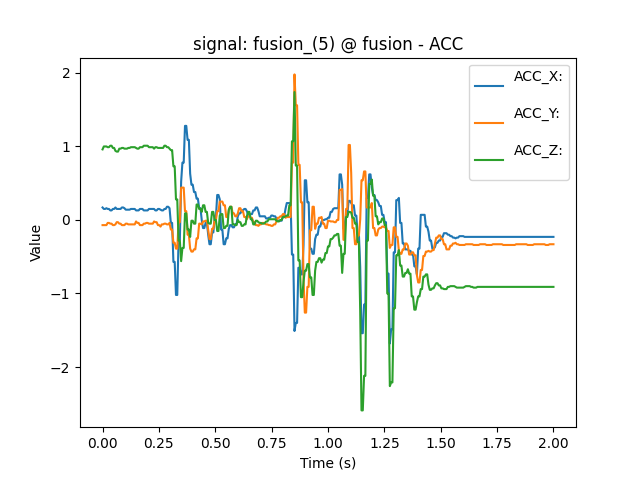
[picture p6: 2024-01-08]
ArduinoExperimentCollection/pop/fusion_(5)/signal_ACC.png

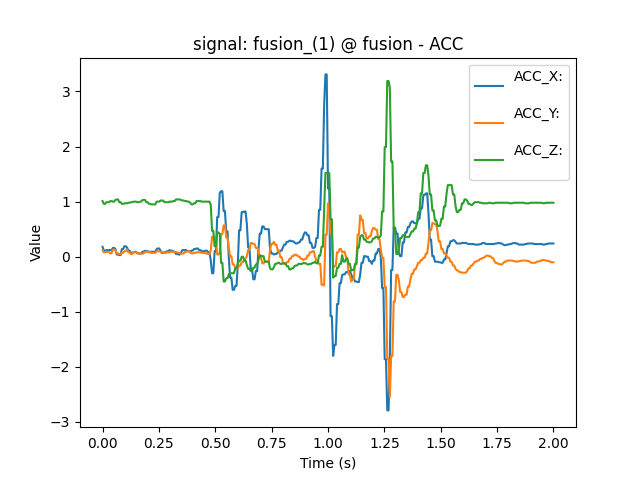
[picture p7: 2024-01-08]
ArduinoExperimentCollection/pop/fusion_(1)/signal_ACC.png

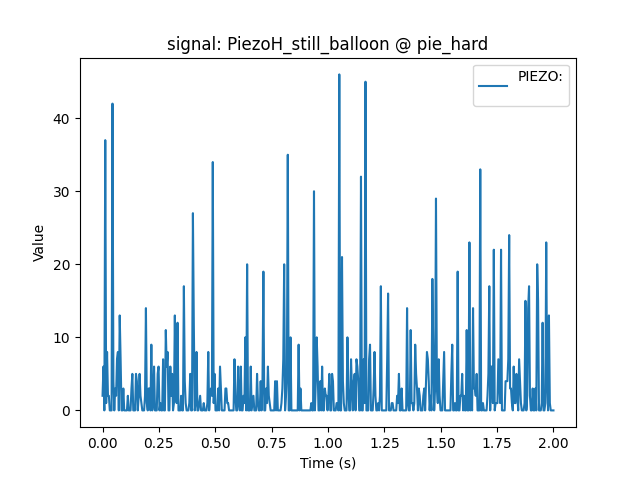
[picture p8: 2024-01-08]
ArduinoExperimentCollection/dataPartyBalloonPiezo/100K-PiozoHard-tapenormal/PiezoH_still_balloon/signal.png

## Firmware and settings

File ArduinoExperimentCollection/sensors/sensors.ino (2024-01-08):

#include "Settings.h"
#include "SensorInterface.h"
#include "proximity_sensor.h"
#include "microphone.h"
#include "piezo.h"
#include "gyroscope.h"
#include "accelerometer.h"
#include "transform.h"

Settings settings;

Gyroscope     gyr;
Accelerometer acc;
Piezo         pie_flex(A2, 50);
Piezo         pie_hard(A3, 500);
Proximity     pro;

short acc_off = 500;
short acc_on =  200;

short piezo_off = 300;
short piezo_on =  700;

short prox_off = 100;
short prox_on = 200;

short mic_off = 8000;
short mic_on = 10000;


// Semi-individual sensors
SensorInterface imu_i ('b', "imu"     , [](int f, unsigned long t){   acc.init(f, t); gyr.init(f, t); }, TestInfo([](){ gyr.test(); return acc.test();     }, acc_off,   acc_on  ),    [](){  acc.del(); gyr.del(); });
SensorInterface pie_f ('e', "pie_flex", [](int f, unsigned long t){   pie_flex.init(f, t);            }, TestInfo([](){ return pie_flex.test();            }, piezo_off, piezo_on),    [](){  pie_flex.del();       });
SensorInterface pie_h ('f', "pie_hard", [](int f, unsigned long t){   pie_hard.init(f, t);            }, TestInfo([](){ return pie_hard.test();            }, piezo_off, piezo_on),    [](){  pie_hard.del();       });
SensorInterface mic_i ('a', "mic"     , [](int f, unsigned long t){   init_mic(f, t);                 }, TestInfo([](){ return test_mic();                 }, mic_off,   mic_on  ),    [](){  del_mic();            });
SensorInterface acc_i ('c', "acc"     , [](int f, unsigned long t){   acc.init(f, t);                 }, TestInfo([](){ return acc.test();                 }, acc_off,   acc_on  ),    [](){  acc.del();            });
SensorInterface gyr_i ('d', "gyr"     , [](int f, unsigned long t){   gyr.init(f, t);                 }, TestInfo([](){ return gyr.test();                 }, acc_off,   acc_on  ),    [](){  gyr.del();            });
SensorInterface pro_i ('g', "pro"     , [](int f, unsigned long t){   pro.init(f, t);                 }, TestInfo([](){ return pro.test();                 }, prox_off,  prox_on ),    [](){  pro.del();            });
SensorInterface clu_i ('t', "Toggle Clutch", [](int f, unsigned long t){transform_init(f, t);         }, TestInfo([](){ return tranfrom_test();            }, 100,       200     ),    [](){  transfrom_delete();   });

// Combinations
TestInfo piezosTests[] = { 
                          TestInfo((TestFunction) [](){return pie_flex.test();}, piezo_off, piezo_on, 1),
                          TestInfo((TestFunction) [](){return pie_hard.test();}, piezo_off, piezo_on, 1)
};
SensorInterface piezos ('h', "piezos" , 
                        [](int f, unsigned long t){   pie_flex.init(f, t); pie_hard.init(f, t); }, 
                        piezosTests, 2, 1800,
                        [](){                         pie_flex.del()     ; pie_hard.del()     ; });

TestInfo piezo_imuTests[] = {
                          TestInfo((TestFunction) [](){return pie_hard.test();}, piezo_off, piezo_on, 1),
                          TestInfo((TestFunction) [](){return      acc.test();}, acc_off,   acc_on,   1)
};
SensorInterface piezos_imu ('i', "pie_hard/imu" , 
                        [](int f, unsigned long t){   pie_hard.init(f, t); acc.init(f, t); }, 
                        piezo_imuTests, 2, 1500,
                        [](){                         pie_hard.del()     ; acc.del()     ; });

TestInfo allTests[] = {
                          TestInfo((TestFunction) [](){return acc.test();      }, acc_off,   acc_on,   3),
                          TestInfo((TestFunction) [](){return pie_hard.test(); }, piezo_off, piezo_on, 2),
                          TestInfo((TestFunction) [](){return pro.test();      }, prox_off,  prox_on,  4),
                          TestInfo((TestFunction) [](){return test_mic();      }, mic_off,   mic_on,   0)
};
SensorInterface all ('j', "all", 
                        [](int f, unsigned long t){   acc.init(f, t); pie_hard.init(f, t); pro.init(f, t); init_mic(f, t); },
                        allTests, 4, 5000,
                        [](){              del_mic(); acc.del()     ; pie_hard.del()     ; pro.del()     ; });

TestInfo allTestsFusion[] = {
                          TestInfo((TestFunction) [](){return acc.test();      }, acc_off,   acc_on,   3),
                          TestInfo((TestFunction) [](){return pie_hard.test(); }, piezo_off, piezo_on, 2),
                          TestInfo((TestFunction) [](){return pro.test();      }, prox_off,  prox_on,  4)
};
SensorInterface fusion ('k', "fusion", 
                        [](int f, unsigned long t){   acc.init(f, t); pie_hard.init(f, t); pro.init(f, t);},
                        allTestsFusion, 3, 5000,
                        [](){              acc.del()     ; pie_hard.del()     ; pro.del()     ; });


void setup() {
  settings.addSensorInterface(&mic_i);
  settings.addSensorInterface(&imu_i);
  settings.addSensorInterface(&acc_i);
  settings.addSensorInterface(&gyr_i);
  settings.addSensorInterface(&pie_f);
  settings.addSensorInterface(&pie_h);
  settings.addSensorInterface(&pro_i);
  settings.addSensorInterface(&piezos);
  settings.addSensorInterface(&piezos_imu);
  settings.addSensorInterface(&all);
  settings.addSensorInterface(&fusion);
  settings.addSensorInterface(&clu_i);


  Serial.begin(115200);
  while(!Serial);

  pinMode(LED_BUILTIN, OUTPUT);
};

void loop() {
  digitalWrite(LED_BUILTIN, HIGH);
  if(Serial.available()>0) {
    char c = Serial.read();
    if(c=='f') {
      int newf = Serial.parseInt();
      settings.setFrequency(newf);
    }
    else if(c=='F') {
      settings.printFrequency();
    }
    else if(c=='i') {
      while(Serial.available()<0) {}
      char interface = Serial.read();
      settings.selectInterface(interface);
    }
    else if(c=='I') {
      settings.printSelectedInterface();
    }
    else if(c=='l') {
      settings.listSensorInterfaces();
    }
    else if(c=='c') {
      int num = Serial.parseInt();
      settings.run_times(num);
    }
    else if(c=='t') {
      int t = Serial.parseInt();
      settings.run_second(t);
    }
    else {
      while(Serial.available()<0)
      Serial.write(c);
    }
  }
}

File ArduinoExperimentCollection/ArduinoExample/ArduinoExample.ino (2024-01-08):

#define STOP_CHAR 'e'

#include "UI.h"
#include "Piezo.h"
#include "IMU.h"
#include "Prox.h"
#include "MIC.h"

UI ui;

void test0() {
  Serial.println(analogRead(A0));
}
void test1() {
  Serial.println(analogRead(A1));
}

void test2() {
  Serial.println("0");
}

SensorInterface a0 ('mic', "mic", test_mic);
SensorInterface a1 ('imu', "imu", test_imu);
SensorInterface a2 ('pie', "pie", test_pie);
SensorInterface a2 ('pro', "pro", test_pro);


void setup() {
  ui.settings.addSensorInterface(&a0);
  ui.settings.addSensorInterface(&a1);
  ui.settings.addSensorInterface(&a2);
  
  piezo::addToUI(&ui);
  imu::addToUI(&ui);
  prox::addToUI(&ui);
  mic::addToUI(&ui);
  
  // put your setup code here, to run once:
  Serial.begin(115200);
  pinMode(A0, INPUT);
}

void loop() {
  // put your main code here, to run repeatedly:
  if(Serial.available()>0) {
    char c = Serial.read();
    if(c=='s') {
      for(int i=0; i<2048; i++) {
        Serial.println(analogRead(A0));
      }
      Serial.println(STOP_CHAR);
    }
    else if (!ui.handleInput(c)) {
      Serial.write(c);
    }
    
  }
}

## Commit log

2023-10-24 Make it possible to select sensors in UI
2023-10-24 Add IMU and propper Piezo suport
2023-10-25 Increase baudrate and add arduino code for mic and proximity sensor
2023-10-27 Arduino code for experiments and data of day 1 of testing
2023-10-29 Move the data text file and make arduino code compile on nano 33 iot
2023-11-05 Implement butterworth filter on arduino and test in python
2023-11-07 Enable filter and make detection work, Disable printing for speedup
2023-11-08 Configurable sensor fusion using sigmoid, no delay
2023-11-09 Delay detection, add script for probebility distribution
2023-11-13 Update sensors.ino
    Updated the thresholds
2023-11-16 Hopefully final plots
    [ResultsIndex.ods]
2023-12-07 Update plots, get code ready for demo
    [ResultsIndex.ods]
2023-12-10 Add CAD Models
    [BlimpCoupling2.stl, BlimpCoupling2_exploded.stl]
2023-12-10 Add CAD Folder to readme
